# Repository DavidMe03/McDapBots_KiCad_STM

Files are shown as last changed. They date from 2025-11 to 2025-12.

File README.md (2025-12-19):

# McDap Bots Pedagogical Robot

This project was created as a capstone project for the University of Virginia Department of Electrical and Computer Engineering. Our goal was to create a small robot which could be programmed by students, for use as a teaching aide in an embedded systems course. This repository contains the hardware files specific to the STM adapter board.

**Authors**
- Colby Wise
- Pratik Pandit
- Austen Yun 
- David Merino
- Marc Rosenthal

**Advisors**: Todd DeLong and Adam Barnes 

**Features at a glance**
- 2 motors (PWM controlled), OLED screen (I2C), reflectance sensor (I2C), bump switches (GPIO), Bluetooth (UART), and infrared sensors (ADC)
- battery charging port and battery voltage display (press button to enable)
- support for TI and STM microcontrollers

## What is contained here
STM32 adapter board for the McDap pedalogical robot. Used to reroute the pins of the main board to the STM Nucleo-G071RB

**Bill of Materials Files**

BOM.xlsx contains a list of all the parts needed for the STM Adapter Board.

Digikey_Parts_List.xlsx can be uploaded to Digikey to select the parts needed for one copy of this board.

## How to use this repository
1. Copy the repository locally to your computer
2. Using KiCad 8.0 (or higher version) open the file `AdapterBoard_McDap.kicad_pro`
3. Generate necessary gerber files and order components
4. Follow the provided construction guide to build the robot

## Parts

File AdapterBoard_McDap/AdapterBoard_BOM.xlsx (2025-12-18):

STM Adapter Board Parts
Id | Designator | Footprint | Quantity | Designation | Supplier | Link | Notes
1 | J1,J2 | PinHeader_2x19_P2.54mm_Vertical | 2 | CN7, CN10 | Digikey | PPPC192LFBN-RC Sullins Connector Solutions | Connectors, Interconnects | DigiKey (https://www.digikey.com/en/products/detail/sullins-connector-solutions/pppc192lfbn-rc/810258) | 2 by 19 female headers for connection to the STM32
2 | J3_J1,J2_J4 | PinHeader_2x10_P2.54mm_Vertical | 2 | LaunchPad | Digikey | PPPC102LFBN-RC Sullins Connector Solutions | Connectors, Interconnects | DigiKey (https://www.digikey.com/en/products/detail/sullins-connector-solutions/PPPC102LFBN-RC/807245) | 2 by 10 female headers for connection to main PCB
Additional Parts
Id | Designator | Footprint | Quantity | Designation | Supplier | Link | Notes
1 |  |  | 2 | Extension Headers | Digikey | ESQ-110-44-T-D Samtec Inc. | Connectors, Interconnects | DigiKey (https://www.digikey.com/en/products/detail/samtec-inc/ESQ-110-44-T-D/7097747) | Tall 2 by 10 female header extenders. These go underneath the headers soldered into J3_J1 and J2_J4.

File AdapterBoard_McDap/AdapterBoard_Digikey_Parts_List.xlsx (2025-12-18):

Digikey Parts List
Manufacturer Part Number | Digikey Part Number | Quantity | Designator | Link | Notes
PPPC192LFBN-RC | S7122-ND | 2 | J1,J2 | PPPC192LFBN-RC Sullins Connector Solutions | Connectors, Interconnects | DigiKey (https://www.digikey.com/en/products/detail/sullins-connector-solutions/pppc192lfbn-rc/810258) | 2 by 19 female headers for connection to the STM32
PPPC102LFBN-RC | S6106-ND | 2 | J3_J1,J2_J4 | PPPC102LFBN-RC Sullins Connector Solutions | Connectors, Interconnects | DigiKey (https://www.digikey.com/en/products/detail/sullins-connector-solutions/PPPC102LFBN-RC/807245) | 2 by 10 female headers for connection to main PCB
ESQ-110-44-T-D | SAM15582-ND | 2 |  | ESQ-110-44-T-D Samtec Inc. | Connectors, Interconnects | DigiKey (https://www.digikey.com/en/products/detail/samtec-inc/ESQ-110-44-T-D/7097747) | Tall 2 by 10 female header extenders. These go underneath the headers soldered into J3_J1 and J2_J4.

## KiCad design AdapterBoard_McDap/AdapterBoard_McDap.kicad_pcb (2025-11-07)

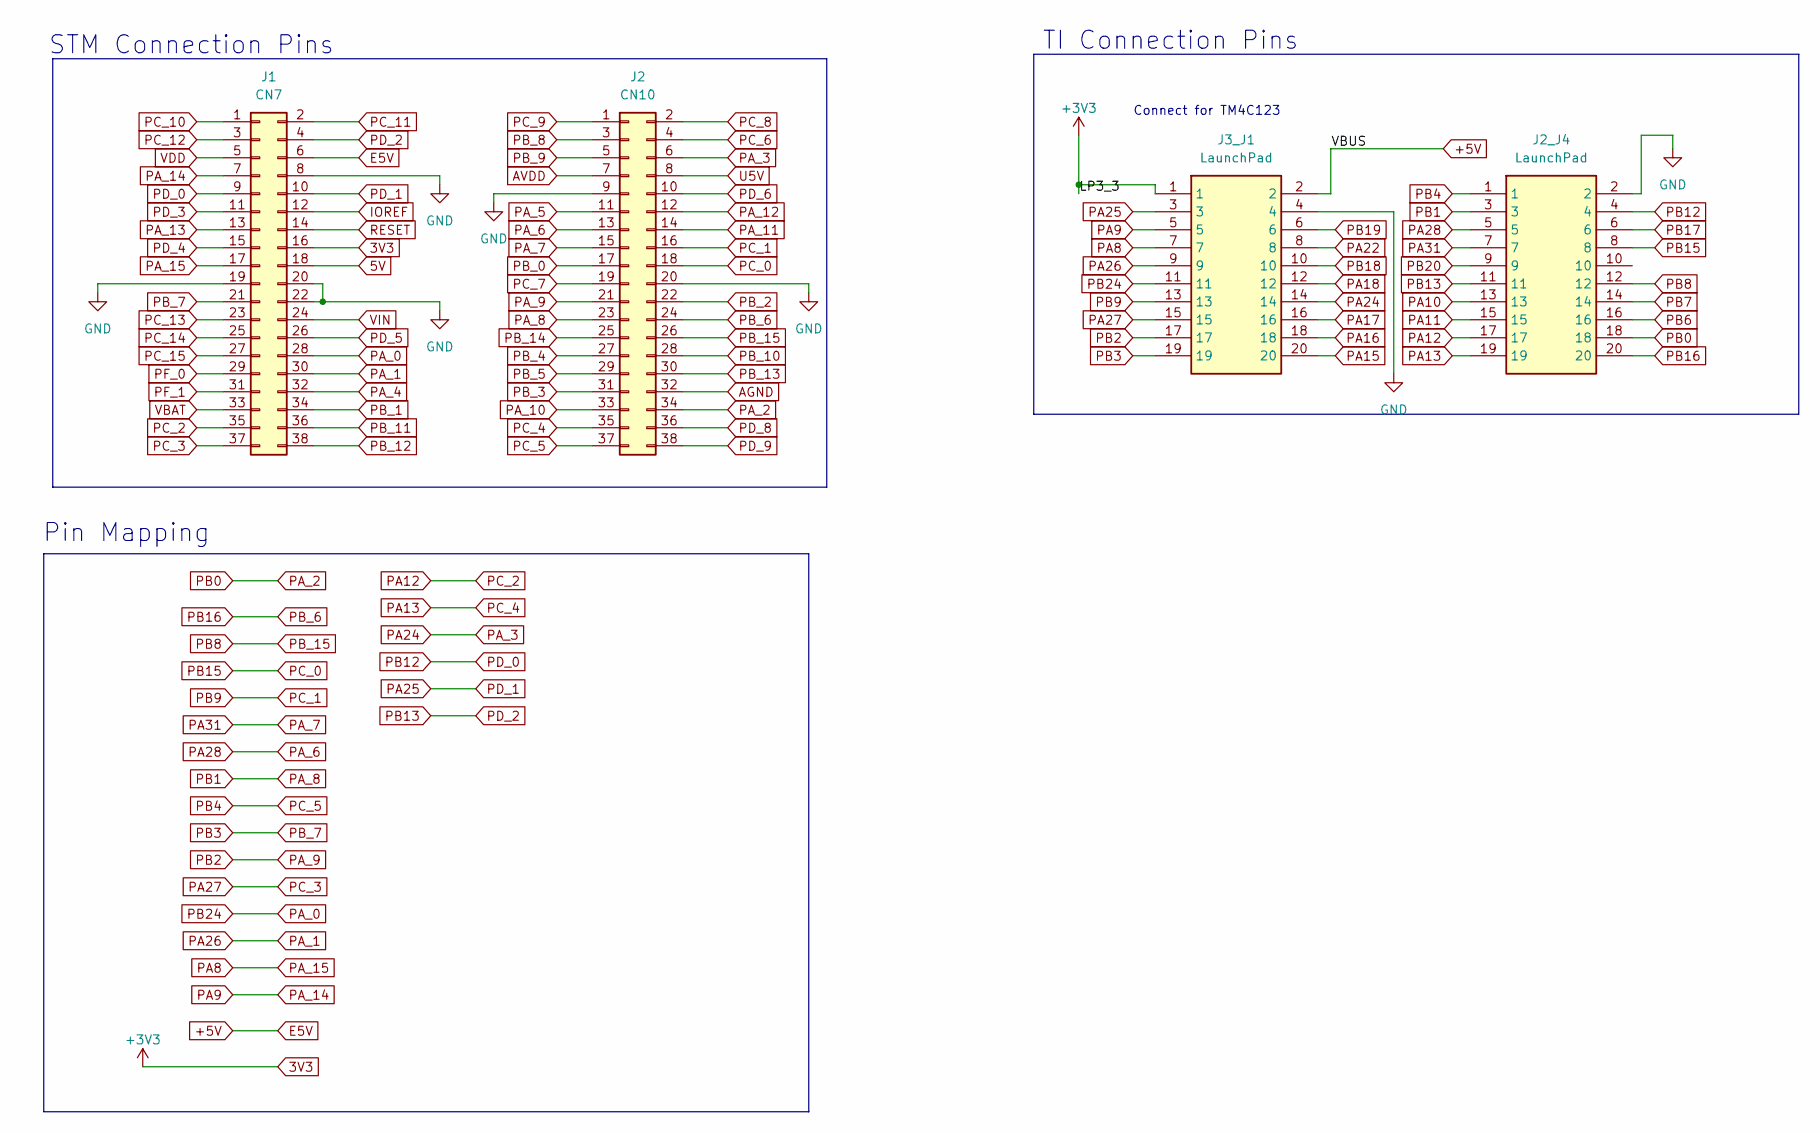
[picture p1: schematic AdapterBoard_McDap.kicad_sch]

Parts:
J1: CN7; PinHeader_2x19_P2.54mm_Vertical
J2: CN10; PinHeader_2x19_P2.54mm_Vertical
J2_J4, J3_J1: LaunchPad; PinHeader_2x10_P2.54mm_Vertical; Mouser Part Number 855-M20-8761042P

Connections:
3V3: J1.16, J3_J1.1
5V: J1.18
+5V: J1.6, J3_J1.2
AGND: J2.32
AVDD: J2.7
GND: J1.8, J1.19, J1.20, J1.22, J2.9, J2.20, J2_J4.2, J3_J1.4
IOREF: J1.12
PA8: J1.17, J3_J1.7
PA9: J1.7, J3_J1.5
PA10: J2_J4.13
PA11: J2_J4.15
PA12: J1.35, J2_J4.17
PA13: J2.35, J2_J4.19
PA15: J3_J1.20
PA16: J3_J1.18
PA17: J3_J1.16
PA18: J3_J1.12
PA22: J3_J1.8
PA24: J2.6, J3_J1.14
PA25: J1.10, J3_J1.3
PA26: J1.30, J3_J1.9
PA27: J1.37, J3_J1.15
PA28: J2.13, J2_J4.5
PA31: J2.15, J2_J4.7
PA_0: J1.28, J3_J1.11
PA_2: J2.34, J2_J4.18
PA_4: J1.32
PA_5: J2.11
PA_8: J2.23, J2_J4.3
PA_9: J2.21, J3_J1.17
PA_10: J2.33
PA_11: J2.14
PA_12: J2.12
PA_13: J1.13
PB3: J1.21, J3_J1.19
PB4: J2.37, J2_J4.1
PB6: J2_J4.16
PB7: J2_J4.14
PB8: J2.26, J2_J4.12
PB9: J2.16, J3_J1.13
PB12: J1.9, J2_J4.4
PB13: J1.4, J2_J4.11
PB15: J2.18, J2_J4.8
PB16: J2.24, J2_J4.20
PB17: J2_J4.6
PB18: J3_J1.10
PB19: J3_J1.6
PB20: J2_J4.9
PB_0: J2.17
PB_1: J1.34
PB_2: J2.22
PB_3: J2.31
PB_4: J2.27
PB_5: J2.29
PB_8: J2.3
PB_9: J2.5
PB_10: J2.28
PB_11: J1.36
PB_12: J1.38
PB_13: J2.30
PB_14: J2.25
PC_6: J2.4
PC_7: J2.19
PC_8: J2.2
PC_9: J2.1
PC_10: J1.1
PC_11: J1.2
PC_12: J1.3
PC_13: J1.23
PC_14: J1.25
PC_15: J1.27
PD_3: J1.11
PD_4: J1.15
PD_5: J1.26
PD_6: J2.10
PD_8: J2.36
PD_9: J2.38
PF_0: J1.29
PF_1: J1.31
RESET: J1.14
U5V: J2.8
VBAT: J1.33
VDD: J1.5
VIN: J1.24

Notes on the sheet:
TI Connection Pins
STM Connection Pins
Pin Mapping
Connect for TM4C123

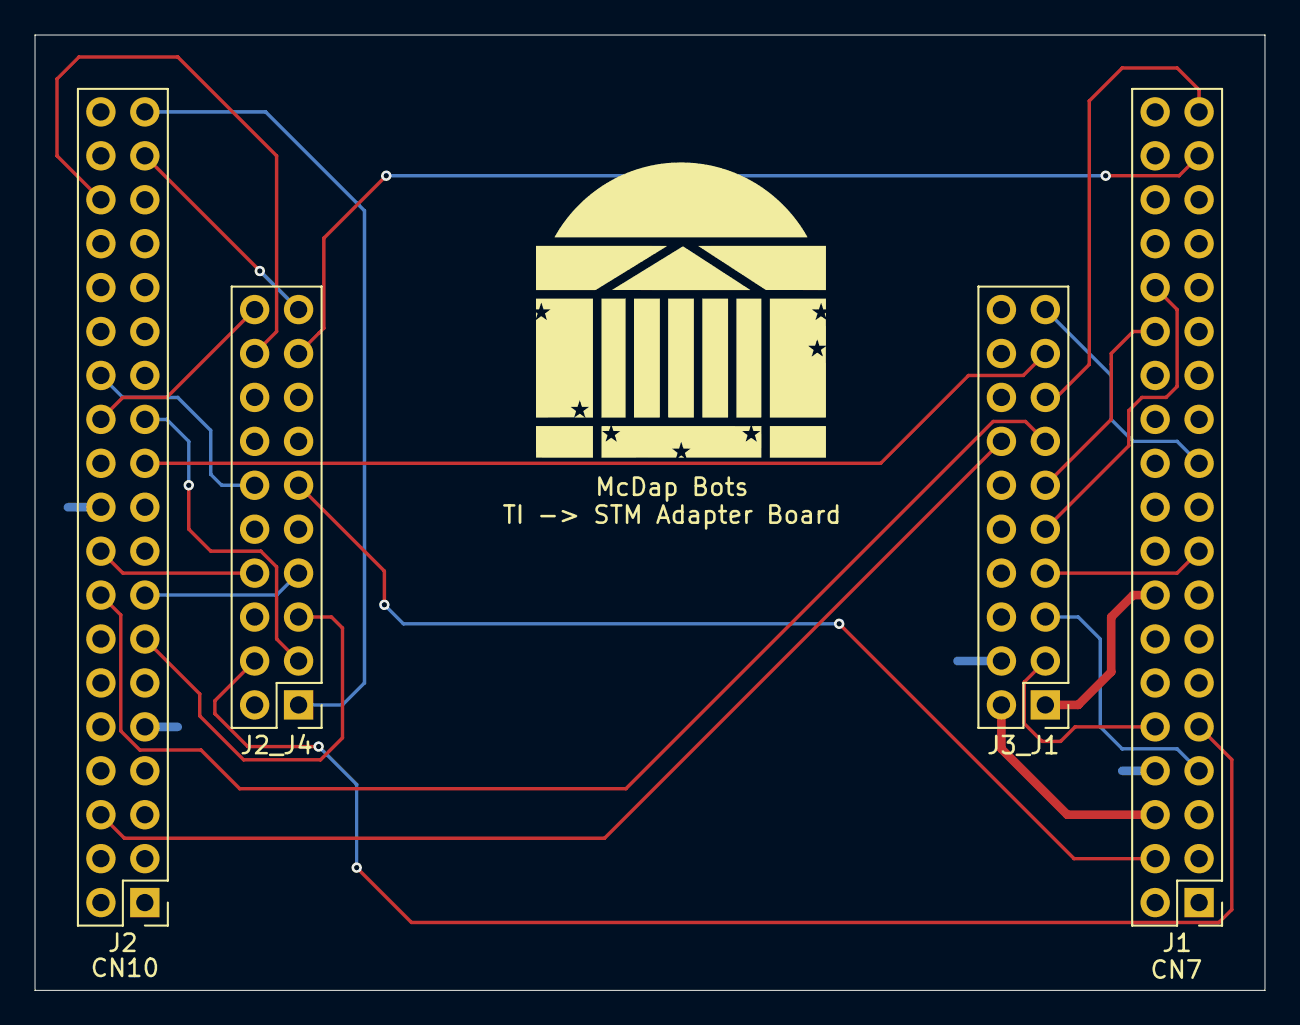
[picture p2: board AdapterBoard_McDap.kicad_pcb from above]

Board: 2 copper layers, 71.1 x 55.2 mm, 5 parts (0 on the bottom side), 25 nets.

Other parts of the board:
J5: RSLK2; RSLK_Chassis

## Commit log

2025-10-08 First commit of KiCad Project
    [AdapterBoard_McDap.kicad_pcb, AdapterBoard_McDap.kicad_sch]
2025-10-08 Initial Additions to schematic & layout
    [AdapterBoard_McDap.kicad_pcb, AdapterBoard_McDap.kicad_sch]
2025-10-16 Added pinmap connections to schematic; Finished layout for adapter board
    [AdapterBoard_McDap.kicad_pcb, AdapterBoard_McDap.kicad_sch]
2025-10-16 minor track changes
    [AdapterBoard_McDap.kicad_pcb]
2025-10-16 Fixing some visual stuff
    [AdapterBoard_McDap.kicad_pcb]
2025-10-16 Added silkscreen image
    [AdapterBoard_McDap.kicad_pcb]
2025-10-16 Add missing pin connection between TI and STM
    [AdapterBoard_McDap.kicad_pcb, AdapterBoard_McDap.kicad_sch]
2025-10-16 Minor silkscreen improvements
    [AdapterBoard_McDap.kicad_pcb]
2025-10-21 Generated gerber files
    [AdapterBoard_McDap-B_Cu.gbr, AdapterBoard_McDap-B_Mask.gbr, AdapterBoard_McDap-Edge_Cuts.gbr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]
2025-11-07 changed pin mappings
    [AdapterBoard_McDap.kicad_pcb, AdapterBoard_McDap.kicad_sch]
2025-11-11 Generated rev 2 gerber files
    [AdapterBoard_McDap-B_Cu.gbl, AdapterBoard_McDap-B_Mask.gbs, AdapterBoard_McDap-Edge_Cuts.gm1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]
2025-12-18 Added BOM and digikey parts files
    [AdapterBoard_BOM.xlsx, AdapterBoard_Digikey_Parts_List.xlsx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]
